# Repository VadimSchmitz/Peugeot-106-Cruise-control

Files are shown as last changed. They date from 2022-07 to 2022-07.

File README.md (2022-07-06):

# Peugeot-106-Cruise-control
This repository is an overview of all the progress and work I have done for an implementation of a "home made" cruise control for my peugeot 106. 

>Disclaimer: Due to this being a very niche project i have not yet put in the time to explain every step and component of the project, if there are any people who want to replicate this feel free to email me at vadimschmitz99@gmail.com
----

## The car
The car is a Peugeot 106 1.1 accent from the year 2000.
The exact specifications of the car can be found [Here](https://www.cars-data.com/en/peugeot-106-accent-1-1-specs/34029). This information is useful to know due to the fact that there were alot of engine options with their own throttle body.

 The electronics and code will probaly most likely work on other specs too however the mounting solution would need to be tweaked for it to work.  

---
## Proof of concept
The initial Proof Of Concept (POC) will be quite simple. To create a POC a few things need to be considered. These are most important Questions and Answers I had before starting the creation of a POC.

### Q) The bare bones functionality of the cruise control?
A) The initial cruise control should have the following functionalities:
- Being able to turn the system on and off
- A way to control the throttle position
- A safety mechanism to turn off the cruise control like a production cruise control (Off switch when brake is pressed)

<br>

### Q) What electronics could to be used to realise these functionalities?
A) After a lot of brainstorming and itterations i came up with the folling electornics that could work as a proof of concetpt. These electronics can be split up in multiple sections.
- Userinterface
  - On/off switch for the control panel (Button)
  - off switch when brake is pressed (Wire into the excisting brake signal)
  - Indicator to see if the system is on or off (Led light)
- The computer that takes inputs and controls the throttle (Arduino)
- Electronical device that can control the Throttle (Servo) 

<br>

### Q) What is the best way to mount the entire contraption?
A) There are multiple things to mount, the userinterface, brake safety, arduino and the device to control the throttle position. After much brain storming i came up with the following solutions
- Userinterface <br  >
There are switches for electric windows in the center console. Since my car does not have the electronic window option the space where the switches would be is blocked off with a plasic plate, this can be removed and the PCB will be mounted there. Picture for reference

    

- Brake safety switch (Not wired or programmed yet) <br  >
  After some prodding around with the brake switch i found out that a reverse switch is used, this means that while it is pressed the circuit is broken, when the brake peddle is pressed the switch will be unpressed and closes the circuit letting 12v go thorugh the system. Therefore all that needs to be done is step the 12v down to 6v and feed this signal into the arduino. the wiring is done directly into the the terminals of the brake switch. 

- Arduino <br  >
  After considering mounting the arduino within the cabin of the car i eventually opted for mounting the arduino within the fuse box.

  

- Servo <br  >
  After a few design iterations I came up with a pulley system. one pulley is connected to the throttle body of the car and the other is connected to a servo which is mounted close by the throttlebody. The final iteration for the proof of concept looks like this

    

    
<br>

---
## Next steps and refinements
Overall the proof of concept works great, I have used it to go to Poland and it has not broken yet. However there are a few things that i want to improve. The aspects of the project could be refined into a real product with the following steps
- Design a custom pcb for the Arduino nano and the user interface
- Laser cut aluminium mounting plate for the pulley
- Make metal or resin printed pulleys 

## Next goal
The main goal right now is creating a true cruise control. This can be done by taking data such as the speed of the car from the CAN BUS of the car and using that data to tweak the throttle position.

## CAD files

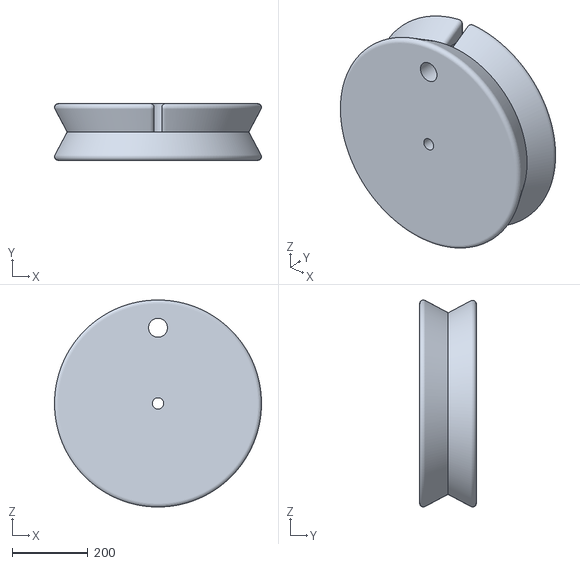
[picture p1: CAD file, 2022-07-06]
stl files/Servo pulley.stl
546.6 x 150.0 x 546.6

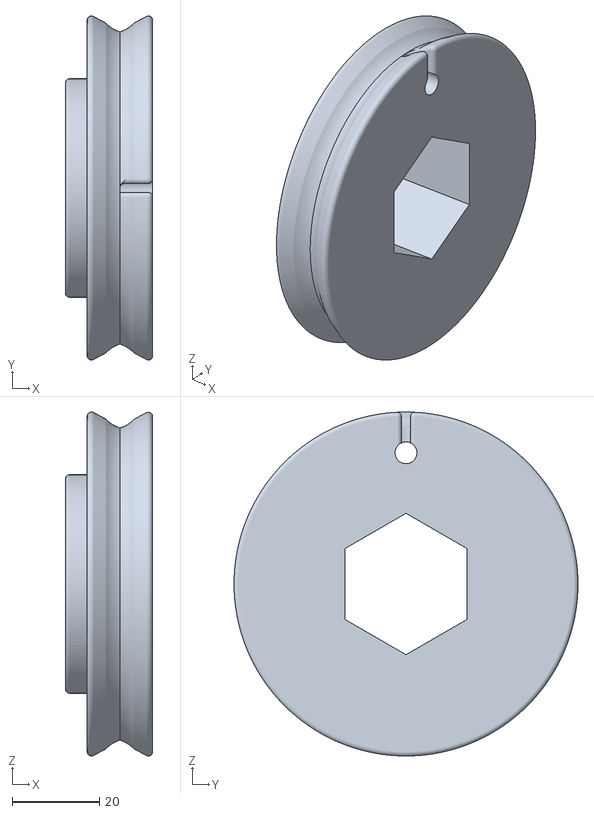
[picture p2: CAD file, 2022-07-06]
stl files/Throttle pulley.stl
20.0 x 78.7 x 78.7

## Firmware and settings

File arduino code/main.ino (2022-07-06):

#include <Servo.h>  // add servo library
Servo myservo; 
int val;   

#define POT_PIN 0
#define POWER_PIN 12
#define BUTTON_PIN 7

byte lastButtonState = LOW;
byte powerState = LOW;

unsigned long debounceDuration = 50; // millis
unsigned long lastTimeButtonStateChanged = 0;

void setup() {
  Serial.begin(9600);
  
  myservo.attach(11);  
  pinMode(POT_PIN, OUTPUT);
  pinMode(BUTTON_PIN, INPUT_PULLUP);
  pinMode(POWER_PIN, OUTPUT);
}

void loop() {
  if (millis() - lastTimeButtonStateChanged > debounceDuration) {
    byte buttonState = digitalRead(BUTTON_PIN);
    if (buttonState != lastButtonState) {
      lastTimeButtonStateChanged = millis();
      lastButtonState = buttonState;
      if (buttonState == LOW) {
        powerState = (powerState == HIGH) ? LOW: HIGH;
        Serial.println(powerState);
        if (powerState == 0){digitalWrite(POWER_PIN, LOW);};
        if (powerState == 1){digitalWrite(POWER_PIN, HIGH);};
      }
    }
  }
  val = analogRead(POT_PIN);            
  val = map(val, 1023, 0, 180, 0);     
  myservo.write(val);                
  delay(100);  
  Serial.println(powerState);
}

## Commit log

2022-07-06 Add project stl files
    [Servo pulley.stl, Throttle pulley.stl]
2022-07-06 Add arduino code
